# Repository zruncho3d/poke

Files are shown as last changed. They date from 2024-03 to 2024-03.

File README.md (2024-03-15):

# Poke: the $1 hotend probe

**Poke** is a flexure-based hotend-mount Z probe for [Printers for Ants](https://3dprintersforants.com/).

Total cost is under $1, print time is ~30m, and weight is ~7g.

| In action | View from below |
| - | - |
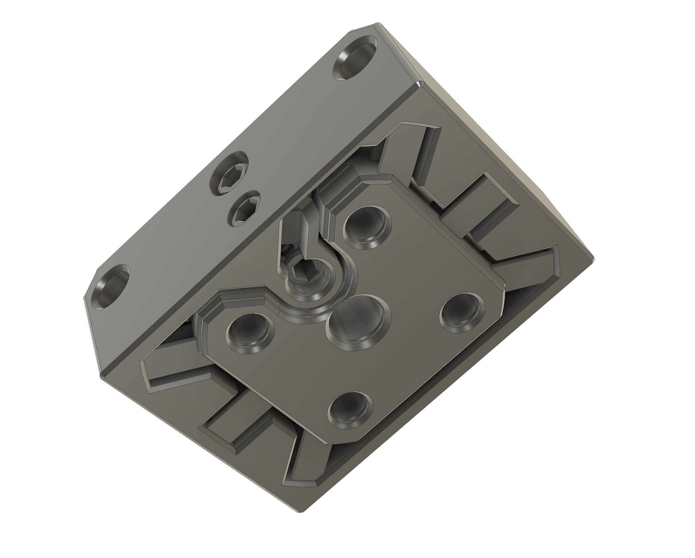
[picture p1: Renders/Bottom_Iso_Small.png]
|  |  |

## What printers are compatible?

Printers that:
* Use the Mini Stealthburner toolhead (or at least share the same hotend mount)
* Have a fully supported bed, like Tri-Zero, Micron, Pandora's Box, SwitchThread, and more
  * Similar to Boop, V0 cantilever beds are a no-go, as they flex too much.
* Have a supported hotend
  * Dragon: :white_check_mark:
  * Revo Voron: not yet, but likely next

Some examples:

| With Dragon | In a Mini Stealthburner | In a MiniSB-compatible cowling |
| - | - | - |
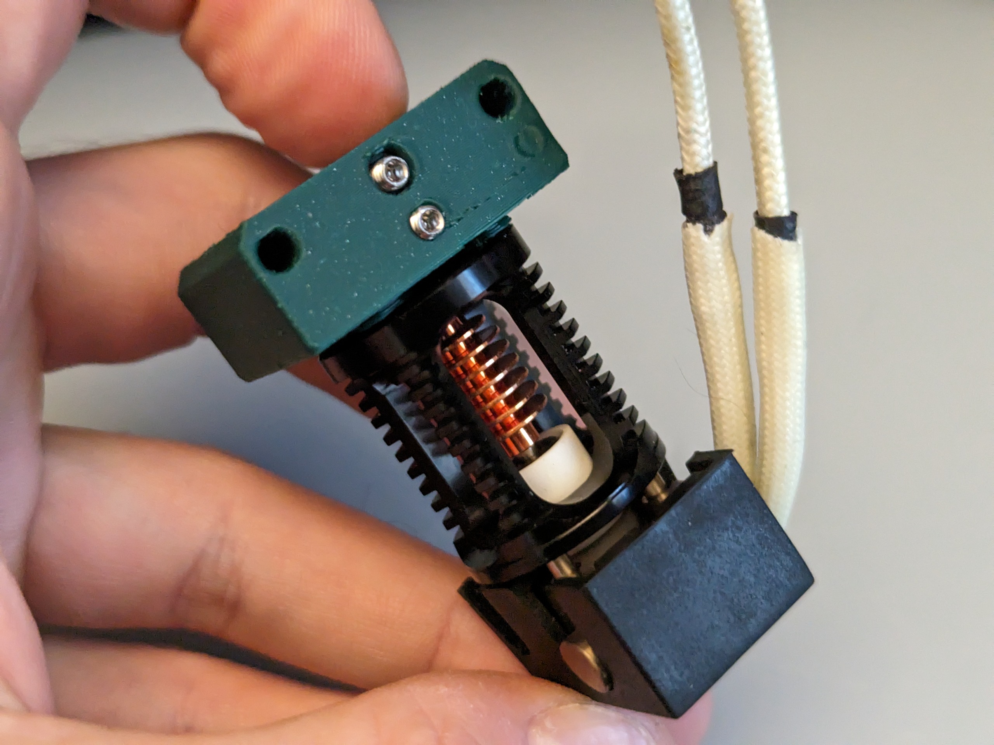
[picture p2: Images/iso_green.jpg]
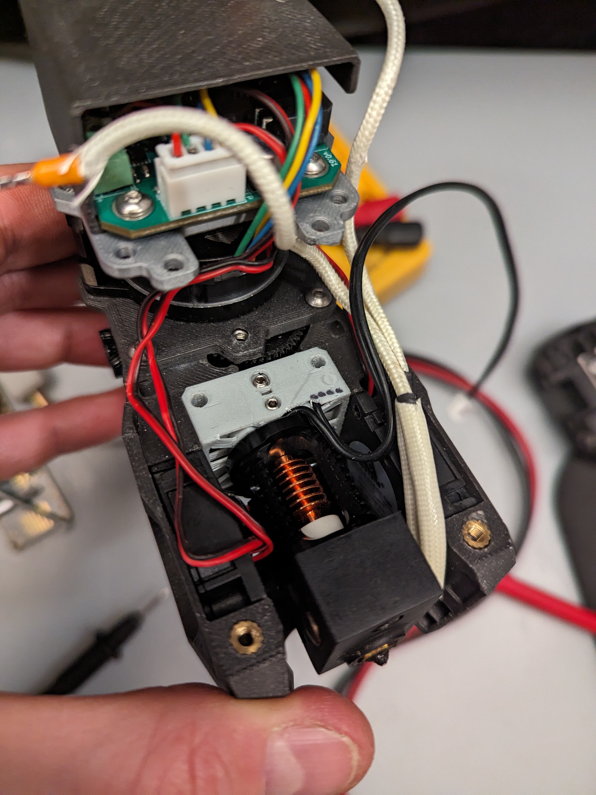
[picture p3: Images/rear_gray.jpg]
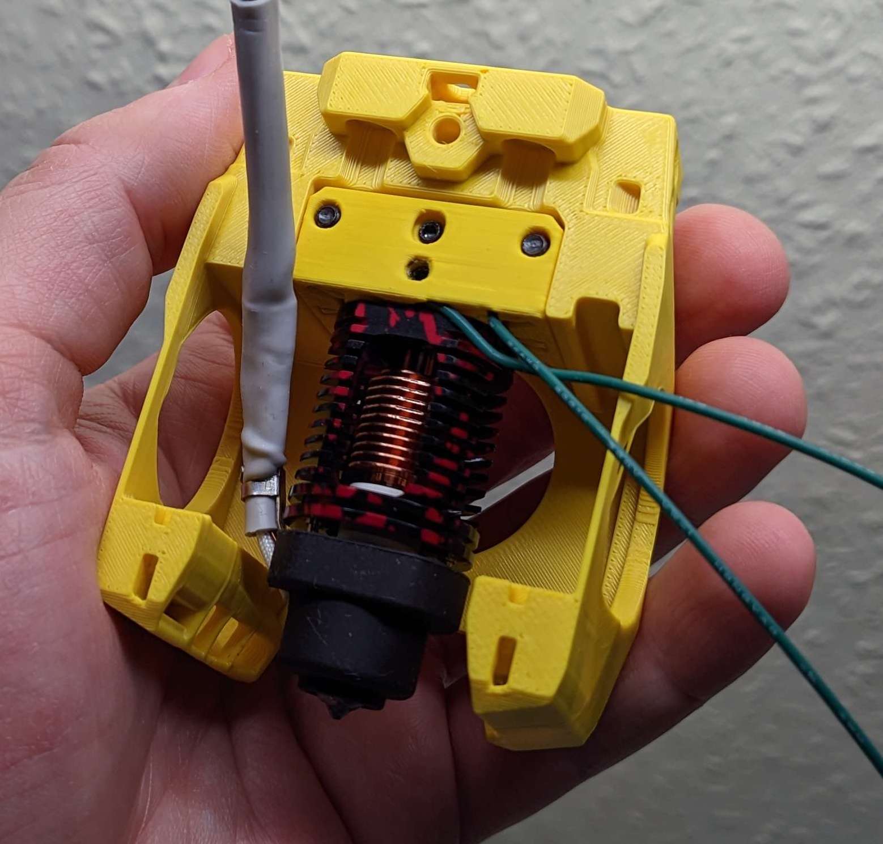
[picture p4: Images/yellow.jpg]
|  |  |  |

The build and installation goes quickly, as only one part is replaced.

## How does it work?

Poke uses:

(1) engineered flexures for constrained up/down motion

(2) set screws that serve triple duty as switch contacts, wire clamps, and preload adjusters.  

An *inner core* fits within an *outer shell*, connected by flexible plastic bridges (*flexures*), and when the hotend presses down, *set screws* break continuity and trigger the probe.  This all happens within one single plastic part.

| Inner Core | Outer Shell | Flexures | Set Screws |
| - | - | - | - |
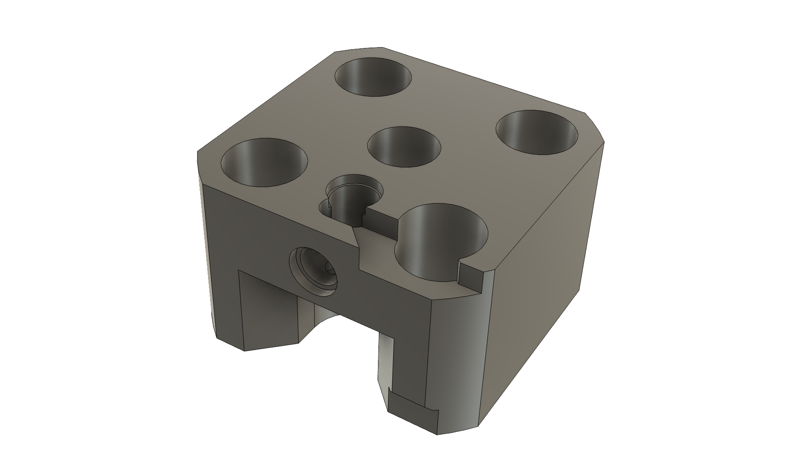
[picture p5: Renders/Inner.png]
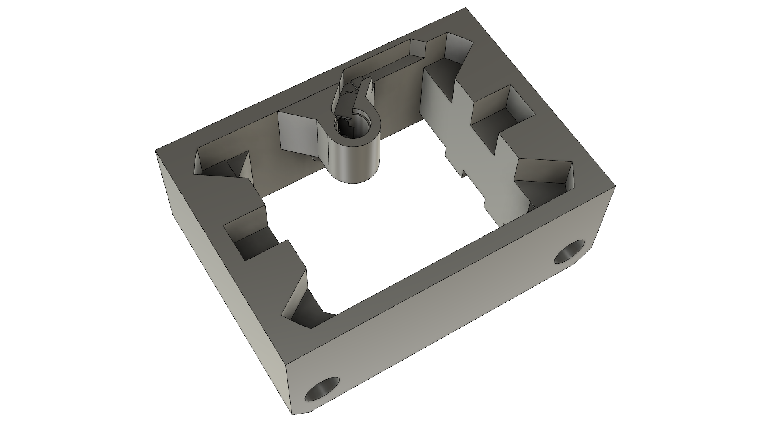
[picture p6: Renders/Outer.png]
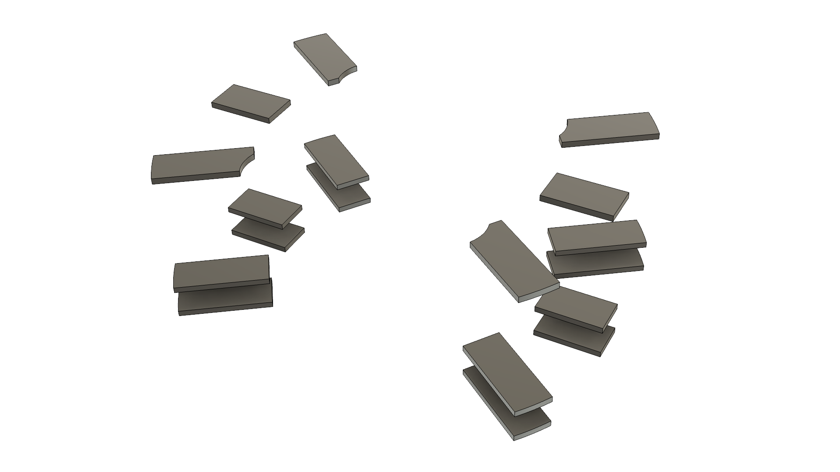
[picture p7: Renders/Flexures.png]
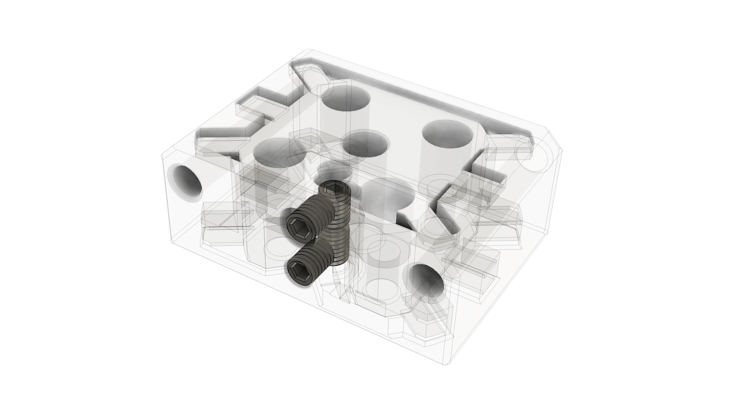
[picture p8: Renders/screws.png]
|  |  |  |  |

The are a ton of ways to enable automatic bed leveling, but **nozzle probing**, where the nozzle tip touches the bed, has real advantages:
* Automatically adjusts after flexplate height changes
* Automatically adjusts after nozzle changes
* Can probe the whole bed area
* Uses simple macros, with no attach/detach macros needed

Lately, [Boop](https://github.com/PrintersForAnts/Boop/tree/main/beta_4), inspired by Voron Tap, has been the premier way to add nozzle probing to [Printers for Ants](https://3dprintersforants.com/), but it comes at a cost: potentially lost travel, a bed shift, added weight, added cost, and worse resonance performance.  

In comparison to Boop, Poke is only 7g vs ~87g (which is a big deal where a toolhead may be 250g!) and only costs $1 vs a $40 Tap kit.

In fairness, hotend support is limited and testing is nowhere near as complete. Hence, the status is Alpha.

## Updates

2024-03-14: Bugfix: Updated to shift filament path back by 0.245 to align with V0.  Thanks `nhchiu`!

## Status: Alpha

What does that mean?

:thumbsup: **Prints well** - for Zruncho at least, at chamber temps, over 10+ hours in 50C+ temps, up to 60C.

:thumbsup: **Documented** - a few people have made them without issue, from just these instructions.

:thumbsup: **Repeatable** - here's the relevant chunks of the an initial `PROBE_ACCURACY` test with 10 samples, which is at microstep-level:

`results: ... range 0.003750 ... standard deviation 0.001008`

:thumbsup: **Clean resonance tests** - Klipper Input Shaper test results seen below.

Test details: Boxed Tri-Zero with custom extrusionless MGN9H X, Hacky Boi toolhead, Papilio Lite extruder, Timmit toolhead board, and custom fixed Boop-center adapter.  Measured with Kusba Pro, at nozzle.

| X | Y |
| - | - |
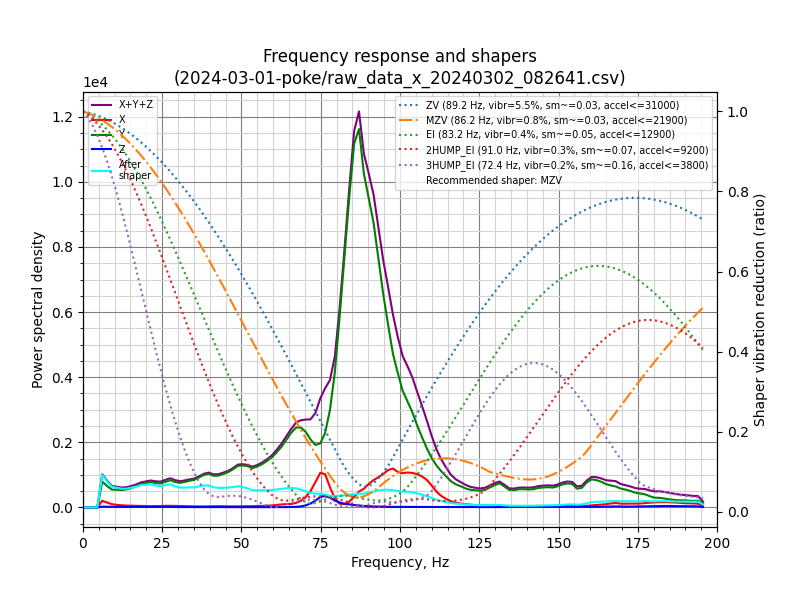
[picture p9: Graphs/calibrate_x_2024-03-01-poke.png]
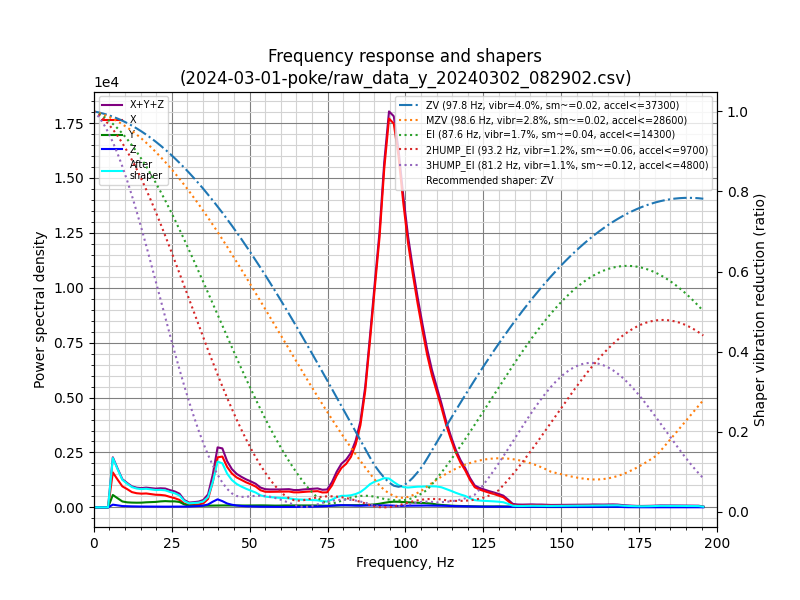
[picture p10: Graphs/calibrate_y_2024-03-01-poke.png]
|  |  |

Beyond 30K accels for X and Y is pretty good.  Expect comparative measurements to come later, against the original fixed hotend mount.

**However**, there are caveats.  As of initial release (March 3 2024), we don't have long-term experience with accuracy or stability.

Plus, hotend support is currently limited - in fact, only Dragon hotends have been tested, and some may never have the space to fit.

This is more of a proof of concept that works, and you should be encouraged to build on it or take the lessons to heart.

## BOM
* **Set Screws**:  4x M3x4 conductive set screws (steel, copper, ... can't be coated alloy or anodized).  M3x3 are fine too, and should help enable ports to smaller spaces.  [Bolt depot link](https://boltdepot.com/Product-Details?product=22896)
* **Wire**:  24AWG zip wire (1.5mm insulation OD, 0.5mm wire ID) works fine.  Any thicker will require mods.
* **Hotend Screws** will be hotend-specific.
  * Dragon: 8mm M2.5 SHCS.   If you have 10-12mm M2.5 handy, adjust the counterbores in the CAD and export.
  * Revo Voron: to come later

## Instructions
* Print the core and spacer using standard Voron settings.  
    * The material must have some flex; ABS is a good choice.
* Install all set screws with formed threads.
    * NOTE: When *forming* threads (using pressure to create threads in small holes in plastic), ensure alignment and push hard at the start.
    * Add upper vertical set screw, until flat with the top surface.  Then do 3 turns (1.5mm)
    * Add lower vertical set screw, until flat with bottom, then do 4 turns (2mm).
    * Add horizontal set screws, until almost flush with outside (with vertical wire channel clear).
* Close the "switch contact" and set the preload.
    * Look at the bottom of the core - the part that faces the hotend.
    * Tighten up to one full turn, until you feel resistance and see the hotend center push away 0.1mm or so from the bottom frame. The tiniest visible amount should be plenty.
    * Push gently on the bottom, while holding the frame, to break the flexure loose.  It may "crack" here from imperfect bridges breaking.
    * The top set screw should move up in the slot, as you press the flexures.  There is 0.4-0.5mm of motion until it hits the max travel, but this should be way more than needed in practice.
* Add wires and tighten horizontal set screws.
    * Strip one end of wire with about 3mm exposed wire length.
    * Feed wire through the open (un-chamfered) internal corner, then over into the space between the set screws.  Lock down the top horizontal screw.  Push down on the wire.  Gently pull tight.
    * Set the other wire length with the same amount exposed.
    * Do the same thing for the bottom wire.
* Add a plug on the other end.
* Test electrical conductivity at the plug end.
    * If no connectivity, turn top set screw slightly.  A bit of resistance (hundreds of ohms) is fine.
    * When you push on the bottom, you should see the circuit open.
* Add spacer and tighten 4x hotend screws.
* Mount on printer!

## Configuration
* Reset your probe’s Z offset.  Since there's low travel until trigger, the new Z offset will depend on the amount of flex in your gantry and toolhead mount.  

## Notes
Core:
* The core is double-notched, so it can be flipped, but by default the wire exit is at the back.
* If you find that the triggering force is too high, you have options to reduce the force:
  * Reduce the preload by adjusting a vertical set screw
  * Clip flexures with flush cutters to reduce the triggering force... there are 18.  
  * Go to the model and remove the inner flexure layer or reduce the flexure width parameter

CAD:
* The main Fusion CAD file uses Configurations, which requires the paid version or a trial to open.  
* Hotend-specific export Fusion files should work on any version.
* The CAD is clean. All sketches, planes, and features are documented, it’s parameterized, and it’s organized via Configurations.  
* New hotend support may be easier than you think, if the hotend has screws in a rectangular grid.

Future work:
* Comparative IS measurements vs original hotend mount
* Long-term stability and probe repeatability testing
* Small internal fillets and chamfers for flexure lifetime and reduced chance of needing breakaway
* A 4mm-ID wave spring at the top might provide more consistent restoring force, especially if the flexure is deformed into the plastic region or experiences force-driven or heat-driven creep.
* Flexure motion limiters

## Support

Like what you see, and want to support more open-source printer development like this?

[Buy me a coffee](https://ko-fi.com/zruncho3d) to show the love and enable future mods and content, stuff like [F0](https://github.com/zruncho3d/f-zero), [T0](https://github.com/zruncho3d/tri-zero), [B0](https://github.com/zruncho3d/boxzero), [X0](https://github.com/zruncho3d/double-dragon), [D0](https://github.com/zruncho3d/DuelingZero), [ZeroPanels](https://github.com/zruncho3d/ZeroPanels), [NoDropNuts](https://github.com/zruncho3d/f-zero/tree/main/STLs/NoDropNuts), [Boop](https://github.com/PrintersForAnts/Boop) improvements, and more!  

For questions, find the Poke user project on the Voron Discord and ask a question.  Don't ping Zruncho.

## Credits

* Flexure layout and concept: `chirpy`
* Flexure proof of concepts that motivated this: `andrewmcgr` (check out [FlexTap](https://github.com/andrewmcgr/FlexTAP)!), `Alexander Þór`.
* Set-screw switch preload and electrical contact design is original - or at least, Z hadn’t seen it before.  But nothing’s truly original anymore, so if you see an earlier reference, set me a note and I'll update this.
* Beta testers that did beta prints: `kevinakasam`, `kyle`, `caza`.
* Gif at the top is courtesy of `kevinakasam`.

:heart: *-Zruncho*

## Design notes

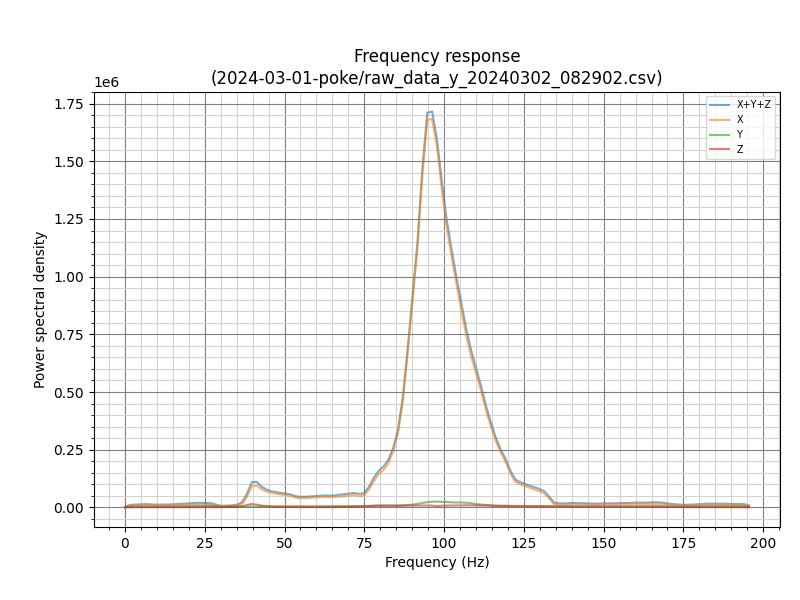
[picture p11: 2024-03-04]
Graphs/y_raw_2024-03-01-poke.png

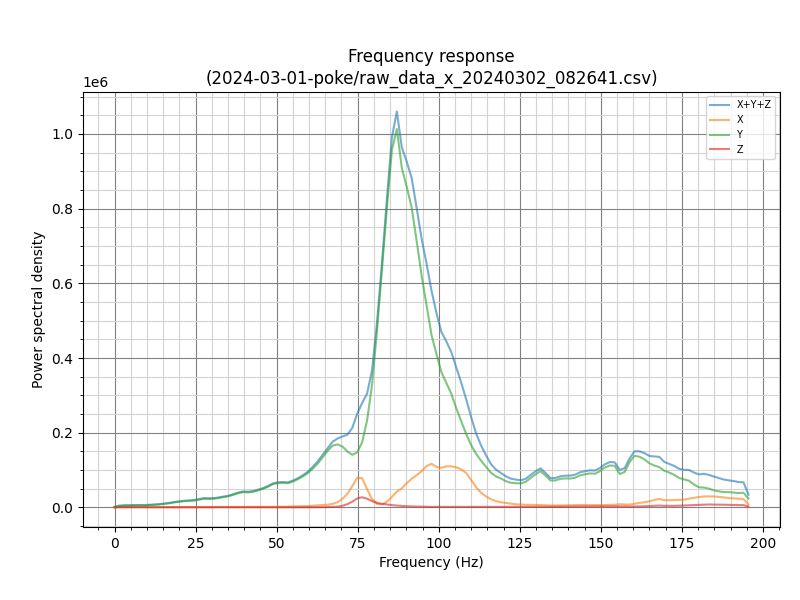
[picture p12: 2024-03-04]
Graphs/x_raw_2024-03-01-poke.png

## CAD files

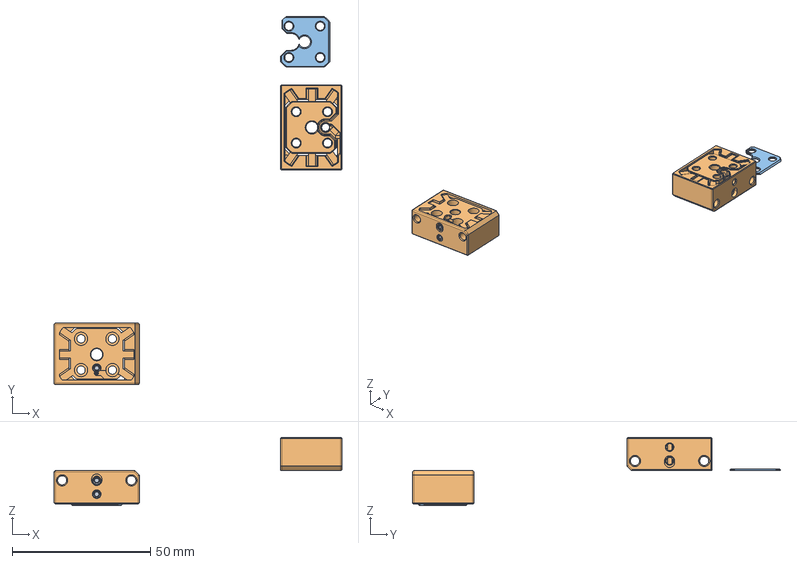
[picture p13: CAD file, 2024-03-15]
CAD/Poke_v15_Dragon.step
103.9 x 132.9 x 24.6 mm
Set Screw m3x4 x 4
Poke x 2
PokeSpacer x 2

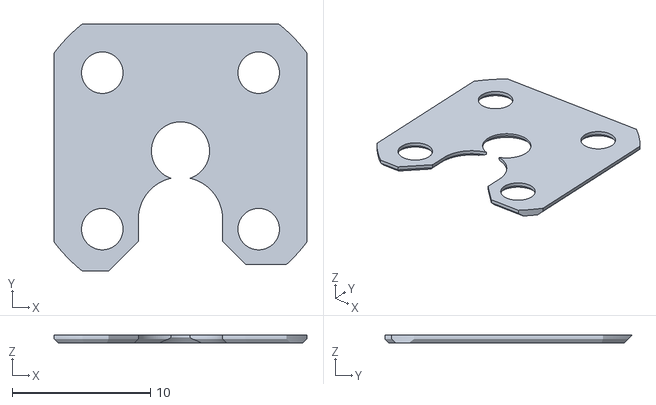
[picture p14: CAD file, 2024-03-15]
STLs/Poke_Spacer_Dragon.stl
18.3 x 17.9 x 0.6

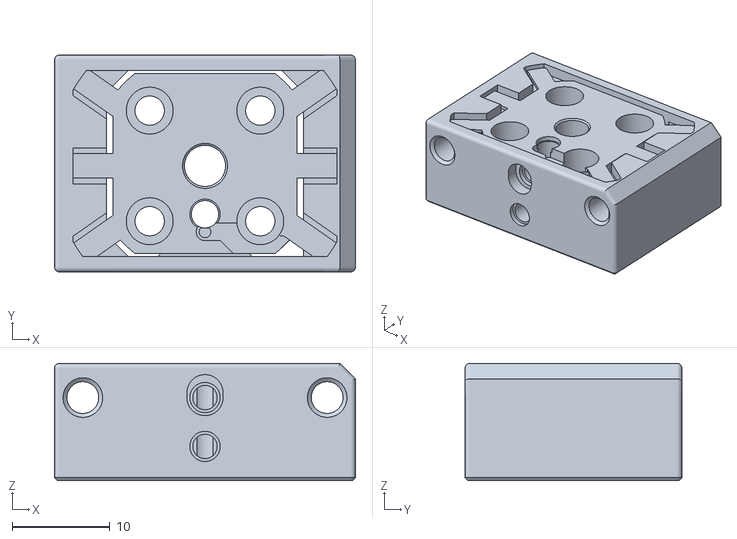
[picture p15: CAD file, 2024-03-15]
STLs/Poke_Core_Dragon.stl
30.8 x 22.2 x 12.0

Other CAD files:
CAD/Poke_v15.f3z
CAD/Poke_v15_Dragon.f3z

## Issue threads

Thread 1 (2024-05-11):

step for Poke_v15.f3z ?

eduncan911, 2024-05-11:
Hey zruncho!  Finally in a position to adapt this to a printer.

I see the step for the Dragon, but the step to the main file seems to be missing?

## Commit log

2024-03-04 First release
    [Poke_Core_Dragon.stl, Poke_Spacer_Dragon.stl, Poke_v13.f3z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]
2024-03-15 Shift filament path back by 0.245 to align with V0
    [Poke_Core_Dragon.stl, Poke_Spacer_Dragon.stl, Poke_v13.f3z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]
